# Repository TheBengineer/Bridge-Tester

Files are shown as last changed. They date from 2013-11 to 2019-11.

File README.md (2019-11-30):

Bridge-Tester
=============

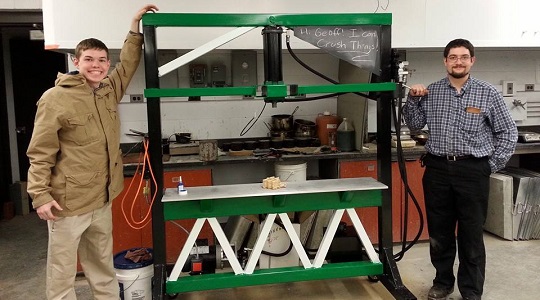
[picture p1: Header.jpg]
Project Image Project Picture


An Open Source bridge tester for popsicle stick bridge competitions.

This was my senior project at Vermont Technical College along with [Carter](
https://github.com/R8driver)

We designed this bridge crusher to be able to crush bridges of up to one meter long, while measuring characturistics about their weight.

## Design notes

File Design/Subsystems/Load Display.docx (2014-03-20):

# I²C Five Digit 7-Segment Display

Ben Holleran March 13, 2014

The following document details how the 7-segment display for the Gordonator bridge tester was designed, and works.

# Table of Contents

# Project Overview

The Gordonator bridge tester is an electro-mechanical senior project at Vermont Technical College. The goal of the project is to build a machine that can measure the force needed to break structures designed by the civil department, Specifically bridges constructed with popsicle sticks with a one meter span. The tester will be capable of replicating the Troitsky Bridge Building Competition at the Concordia University in Canada.

The Load Display subsystem will be displaying the force exerted on the bridge by the piston. Since the expected load is in excess of 9,999 LB, and less than 99,999 LB the display will have 5 digits. The display will also have 4” letters so the winning number can be seen from the back of the room.

# System Overview

## System Diagram

## System Description

As seen in the above system diagram, the display will be broken into 5 identical systems, each with a different IIC address. Each cell will have a single 7-segment display and the circuit needed to drive it. This will allow for easy replacement, and ease of design.

## Design Process

## Inception

The first step in the design process for the Load Display was its inception. There needed to be some form of a display to show the crowds how much force each bridge could hold. Some competitions do not need a load display, specifically high school competitions where weight of some kind is added incrementally until the bridge breaks. The weight can then be added up empirically by measuring the amount of water, or counting up how many weights were added. Since this tester will be using a hydraulic cylinder to provide force, allowing much higher loads than practical by the added weight method, there needs to be a display.

Research

The current tester at the Troitsky Bridge Building Competition was researched, and found to have a display only 1” high. Numerous people who have attended the competition have expressed that the display is too small, and is not visible from the seating area.

The problem was discussed with fellow students, professors, Industry professionals, and all of that was held together with queries to Google.

While researching current existing technology a few interesting discoveries were made:

- Many 2” and 3” clocks exist premade, but as clocks only have 4 digits.
- Many of the chips designed to run 7 segment displays are designed to run clocks.
- There are large numerical displays that are not clocks, but they are very expensive. The cheapest being around $500
- DigiKey sells individual 7 segments of all sizes.
- Texas instruments makes a nice IIC shift register suitable for running a single digit.

While researching communications it was determined that there were a few different technologies that were suitable.

- Serial
  - Single receiver, would require a MUX to run the separate digits
  - Very easy to use
- IIC
  - Multiple receivers
  - More difficult to use
- Direct IO
  - Easy to use
  - Needs a complicated circuit
  - Not enough pins

Brainstorming

After the available technologies were researched, the design was brainstormed to determine the best way to build the load display. It was determined that there were not enough pins on the Pi to do Direct IO and that a MUX circuit would be harder to make than the other available solutions. Serial was disqualified since it can have only one receiver, and that would make that receiver need to have enough pins to run all the displays, bringing back the Direct IO problem. There is multi receiver serial, but if going that route, IIC makes for a much better solution since it is in essence multi receiver serial, with the protocols already in place.

At one point it was considered to rate each system based on a number of criteria and pick the best one numerically, but those charts tend to be bullshit, so we just discussed the systems until it was clear which ones were less favorable, and then made an educated gut decision.

In the case of displays, it was originally thought that the best way to make a display would be to make the 7-segments from scratch using 5mm LEDs and large circuit boards. This was dismissed as too complicated and time consuming. Hacking a Walmart display was considered to be a bad idea in general, and all in all, the best solution seemed to be to buy premade 7-segments.

## Analysis

Once the 7-segments were chosen, the forward voltages of the LED arrays were measured and plotted on a Gaussian bell curve. This was then used to get a statistical voltage for the displays, allowing a more accurate current limiting resistor to be added.

The Datasheet said that the forward voltage on the 7-segents might be as low as 8V, meaning the resistor would have 4V from the 12V line across it. The calculated value to regulate to 60mA meant that if the forward voltage of the LEDs was 10V, the upper limit in the datasheet, there would only be 30mA going through the LEDs. This would significantly cut down on visibility. By using the voltage determined from the Gaussian bell curve, a resistor value was found that would put 70% of the LEDs at 50mA while being 90% sure that no LED would have over 60mA

Design

It was determined that the best way to construct a Load display would be to purchase 4” 7-segment displays from DigiKey, buy an IIC 7-segment driver chip from TI, create a board to connect everything, and then use a Python program running on the Pi to tell it what number to display over IIC.

## Testing

Once the Raspberry Pi was up and running, testing began on the chips and 7 segment displays. At first there were many unknown errors. Many of them proved to be problems with understanding of the IIC bus and driver issues on the Pi, but those were quickly sorted out. One of the more difficult errors to track down was a bad solder joint on the surface mount driver chips. After this discovery, all pins on all the chips were resoldered by hand and individually checked for continuity and shorting.

## Documentation

At all stages of the process, notes were taken in a project notebook. Some documentation for code was added to the GIT repository as commits. These comments were clear so that when looked at later, they would be easily understood.

## Project Management

Most of the project management: Task assignment, issue tracking, timeline, and file management, was all done by GitHub, a free online project management website. This tool will continue to be used throughout the project and will allow other people interesting in the design of the project to see what decisions were made.

# Conclusion

This subsystem is on track to being finished for its integration with the main project. The goal is to have a rock solid subsystem, so that any issues will be from its integration to the rest of the system, rather than issues with the subsystem itself.

I²C Five Digit 7-Segment Display Ben Holleran March 13, 2014

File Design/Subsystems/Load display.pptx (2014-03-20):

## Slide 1

88888

Load display

Power

IIC data line

GPIO Buffer

Raspberry PI

Single Digit

8

IIC Shift Register
TIPC2810

12 V

5 V

Individual segments. Switched to ground and current limited.

GND

IIC lines

Chip has 3 bits to program address. Need 5 addresses, one for each digit.

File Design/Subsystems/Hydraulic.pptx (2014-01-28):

## Symbols

Hydraulic
Motor

Pump

Cylinder

Reservoir

Pressure Relief

Check Valve

Filter

Valve

## Hydraulic Subsystem

1 ½ NPT

Valve has built in pressure relief

¾ NPT

½ NPT

¾-16

¼ NPT

Pressure Sensor

## Fittings List

1 ½ NPT

¾ NPT

½ NPT

¾-16

¼ NPT

Valve has built in pressure relief

Male to Male

½ - ½ - ¼ T

Pressure Sensor

5” pipe

¾ -16 m > ¾ NPT M

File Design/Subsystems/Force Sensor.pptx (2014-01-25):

## Force Sensor Subsystem Diagram

+12V

I²C ADC
24 bit

To I²C Master

Sensor

Address Config

¼ NPT

## Force Sensor Subsystem Schematic

+12V

I²C ADC
24 bit

Sensor

¼ NPT

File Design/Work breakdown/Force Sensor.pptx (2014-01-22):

## Force Sensor Subsystem Diagram

To Piston

I²C A to D Converter

Pressure Sensor

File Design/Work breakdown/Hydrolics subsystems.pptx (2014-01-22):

## Hydraulics Subsystem

Pump

Piston

Switch

Pressure Sensor

Pressure relief Valve

Motor

Reservoir

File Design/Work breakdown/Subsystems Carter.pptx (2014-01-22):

## Work Breakdown

Areas of Responsibility | | | | Mechanical
Ben | | Carter | | Electrical
Hydraulics | | Frame | | Software
Force Sensor | | Monitor and 7-Segment
HDMI Display GUI | | HDMI Display GUI
Mounting Points on Frame | | Mounting Points on Frame
Website | | Website

## Frame

Final top structure design pending on cylinder used

Exostructure made of 3in hollow steel tubing

40in span between trusses for Troisky compatible bridges and max strength

40in

3 triangular trusses for structural support made of 2in hollow steel tubing

Wheels for easy mobility of unit

## Hydraulics Subsystem

Pump

Piston

Switch

Pressure Sensor

Pressure relief Valve

Motor

Reservoir

## 7-Segment Display Subsystem

V+ ~20V

7-Seg
Digit

X5

Input from Pi
Over GPIO

I2C
7-Seg Driver

7-Seg Driver requires 11V forward. I2C driver outputs 5V. Darlington Array is used to boost voltage to 7-Segment Digits.

Darlington Array

Ground

## LCD Monitor Subsystem

Inputs from sensors

Raspberry Pi

GPIO

Deformation

HDMI

READOUTS

Force

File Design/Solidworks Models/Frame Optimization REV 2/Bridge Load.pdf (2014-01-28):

Vermont technical College
Company Address Line 2]

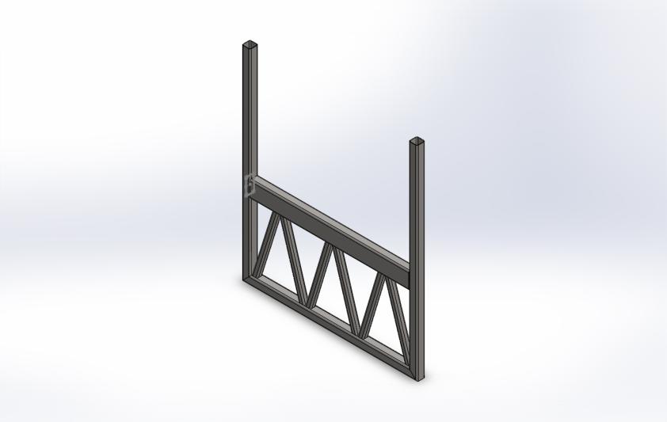
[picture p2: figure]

Analyzed with SolidWorks Simulation | Simulation of Main Frame | 1

# Simulation of Main Frame

Date: Wednesday, January 22, 2014 Designer: Carter Mealey, Ben Holleran Study name: Bridge
Analysis type: Static

## Table of Contents

## Description

No Data

Vermont technical College | Carter Mealey, Ben Holleran

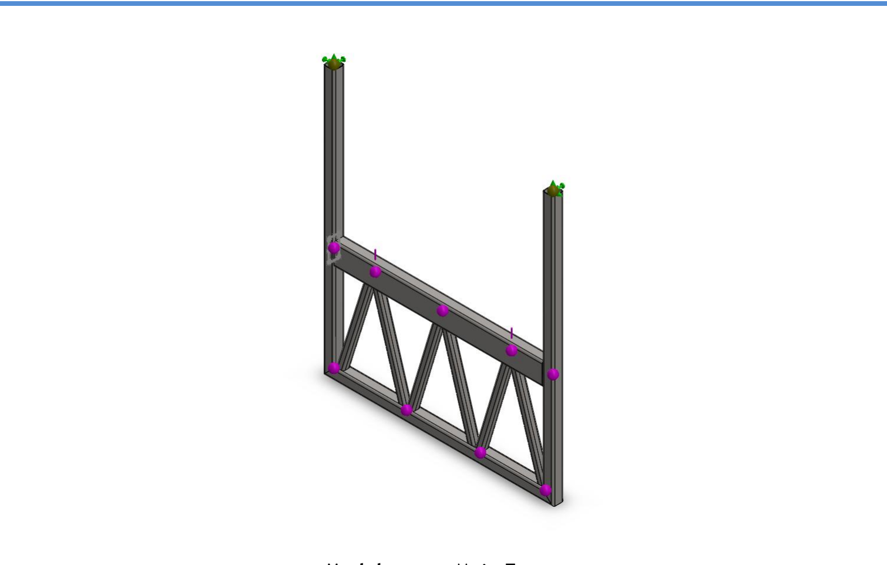
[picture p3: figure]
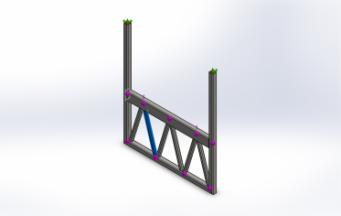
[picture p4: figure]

Analyzed with SolidWorks Simulation | Simulation of Main Frame | 2

## Assumptions

## Model Information

Model name: Main Frame
Current Configuration: Default<As Machined>

### Beam Bodies:

Document Name and Reference | Formulation | Properties | Document Path/Date Modified
Beam-1(Truss Trim[2]) | Beam – Uniform C/S | Section Standard-Section Area: 544.265in^2 Length:636.35mm Volume:0.000346335m^3 Mass Density:7800kg/m^3 Mass:2.70141kg Weight:26.4738N | \\vtcfiles\shared\ELM\ELM 4701\Bridge Tester\Design\Solidworks Models\Frame Optimization REV 2\Main Frame.SLDPRT Jan 22 00:54:07 2014

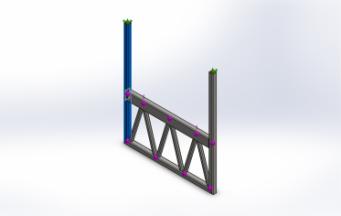
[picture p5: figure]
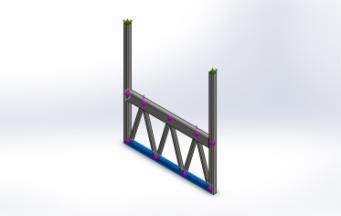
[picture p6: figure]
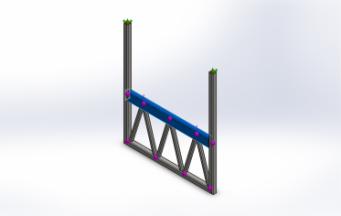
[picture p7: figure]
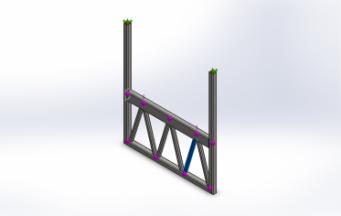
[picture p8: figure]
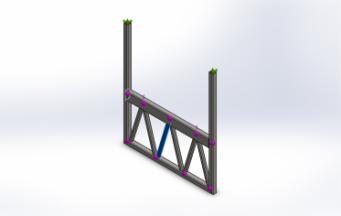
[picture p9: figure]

Analyzed with SolidWorks Simulation | Simulation of Main Frame | 3
Beam-2(Bottom miter 2[2]) | Beam – Uniform C/S | Section Standard-ansi inch/square tube/3 x 3 x 0.25 Section Area: 866.845in^2 Length:1828.8mm Volume:0.00158529m^3 Mass Density:7800kg/m^3 Mass:12.3652kg Weight:121.179N | \\vtcfiles\shared\ELM\ELM 4701\Bridge Tester\Design\Solidworks Models\Frame Optimization REV 2\Main Frame.SLDPRT Jan 22 00:54:07 2014
Beam-3(Bottom miter 2[1]) | Beam – Uniform C/S | Section Standard-ansi inch/square tube/3 x 3 x 0.25 Section Area: 1670.35in^2 Length:1524mm Volume:0.00254566m^3 Mass Density:7800kg/m^3 Mass:19.8561kg Weight:194.59N | \\vtcfiles\shared\ELM\ELM 4701\Bridge Tester\Design\Solidworks Models\Frame Optimization REV 2\Main Frame.SLDPRT Jan 22 00:54:07 2014
Beam-4(Deck trim) | Beam – Uniform C/S | Section Standard-ansi inch/rectangular tube/3 x 2 x 0.25 Section Area: 1350.71in^2 Length:1447.8mm Volume:0.00195556m^3 Mass Density:7800kg/m^3 Mass:15.2534kg Weight:149.483N | \\vtcfiles\shared\ELM\ELM 4701\Bridge Tester\Design\Solidworks Models\Frame Optimization REV 2\Main Frame.SLDPRT Jan 22 00:54:07 2014
Beam-5(Truss Trim[5]) | Beam – Uniform C/S | Section Standard-Section Area: 544.265in^2 Length:636.35mm Volume:0.000346335m^3 Mass Density:7800kg/m^3 Mass:2.70141kg Weight:26.4738N | \\vtcfiles\shared\ELM\ELM 4701\Bridge Tester\Design\Solidworks Models\Frame Optimization REV 2\Main Frame.SLDPRT Jan 22 00:54:07 2014
Beam-6(Truss Trim[3]) | Beam – Uniform C/S | Section Standard-Section Area: 544.265in^2 Length:636.35mm Volume:0.000346335m^3 Mass Density:7800kg/m^3 Mass:2.70141kg Weight:26.4738N | \\vtcfiles\shared\ELM\ELM 4701\Bridge Tester\Design\Solidworks Models\Frame Optimization REV 2\Main Frame.SLDPRT Jan 22 00:54:07 2014

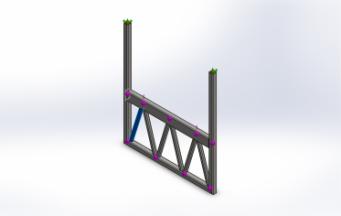
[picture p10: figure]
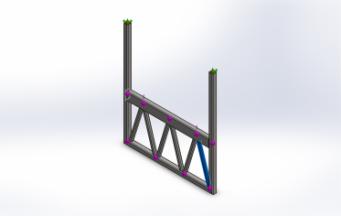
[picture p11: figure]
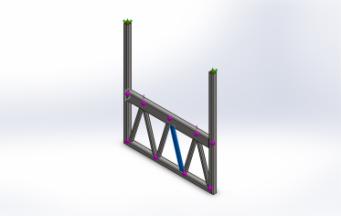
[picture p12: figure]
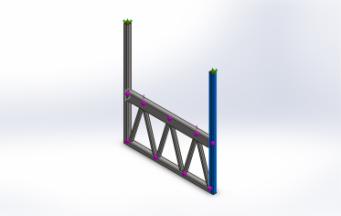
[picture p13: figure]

Analyzed with SolidWorks Simulation | Simulation of Main Frame | 4
Beam-7(Truss Trim[1]) | Beam – Uniform C/S | Section Standard-Section Area: 544.265in^2 Length:638.672mm Volume:0.000347599m^3 Mass Density:7800kg/m^3 Mass:2.71127kg Weight:26.5704N | \\vtcfiles\shared\ELM\ELM 4701\Bridge Tester\Design\Solidworks Models\Frame Optimization REV 2\Main Frame.SLDPRT Jan 22 00:54:07 2014
Beam-8(Truss Trim[6]) | Beam – Uniform C/S | Section Standard-Section Area: 544.265in^2 Length:638.672mm Volume:0.000347599m^3 Mass Density:7800kg/m^3 Mass:2.71127kg Weight:26.5704N | \\vtcfiles\shared\ELM\ELM 4701\Bridge Tester\Design\Solidworks Models\Frame Optimization REV 2\Main Frame.SLDPRT Jan 22 00:54:07 2014
Beam-9(Truss Trim[4]) | Beam – Uniform C/S | Section Standard-Section Area: 544.265in^2 Length:636.35mm Volume:0.000346335m^3 Mass Density:7800kg/m^3 Mass:2.70141kg Weight:26.4738N | \\vtcfiles\shared\ELM\ELM 4701\Bridge Tester\Design\Solidworks Models\Frame Optimization REV 2\Main Frame.SLDPRT Jan 22 00:54:07 2014
Beam-10(Bottom miter 1[2]) | Beam – Uniform C/S | Section Standard-ansi inch/square tube/3 x 3 x 0.25 Section Area: 866.845in^2 Length:1828.8mm Volume:0.00158529m^3 Mass Density:7800kg/m^3 Mass:12.3652kg Weight:121.179N | \\vtcfiles\shared\ELM\ELM 4701\Bridge Tester\Design\Solidworks Models\Frame Optimization REV 2\Main Frame.SLDPRT Jan 22 00:54:07 2014

Analyzed with SolidWorks Simulation | Simulation of Main Frame | 5

## Study Properties

Study name | Bridge
Analysis type | Static
Mesh type | Beam Mesh
Solver type | Direct sparse solver
Inplane Effect: | Off
Soft Spring: | Off
Inertial Relief: | Off
Incompatible bonding options | Automatic
Large displacement | Off
Compute free body forces | On
Result folder | SolidWorks document (\\vtcfiles\shared\ELM\ELM4701\Bridge Tester\Design\Solidworks Models\Frame Optimization REV 2)

## Units

Unit system: | SI (MKS)
Length/Displacement | mm
Temperature | Kelvin
Angular velocity | Rad/sec
Pressure/Stress | N/m^2

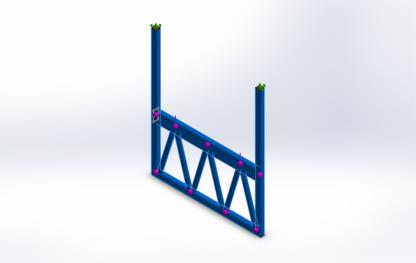
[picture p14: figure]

Analyzed with SolidWorks Simulation | Simulation of Main Frame | 6

## Material Properties

Model Reference | Properties | Components
| Name: Plain Carbon Steel Model type: Linear Elastic Isotropic Default failure criterion: Unknown
| Yield strength: 2.20594e+008 N/m^2 Tensile strength: 3.99826e+008 N/m^2 Elastic modulus: 2.1e+011 N/m^2 Poisson's ratio: 0.28 Mass density: 7800 kg/m^3 Shear modulus: 7.9e+010 N/m^2 Thermal expansion coefficient: 1.3e-005 /Kelvin

SolidBody 1(Truss
Trim[2])(Main Frame),
SolidBody 2(Bottom miter
2[2])(Main Frame),
SolidBody 3(Bottom miter
2[1])(Main Frame),
SolidBody 4(Deck trim)(Main Frame),
SolidBody 5(Truss
Trim[5])(Main Frame),
SolidBody 6(Truss
Trim[3])(Main Frame),
SolidBody 7(Truss
Trim[1])(Main Frame),
SolidBody 8(Truss
Trim[6])(Main Frame),
SolidBody 9(Truss
Trim[4])(Main Frame),
SolidBody 10(Bottom miter
1[2])(Main Frame)

Curve Data:N/A

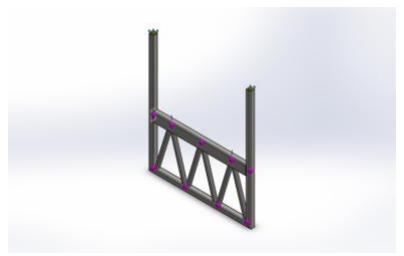
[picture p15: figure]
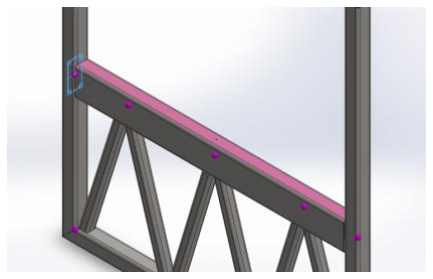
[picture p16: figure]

Analyzed with SolidWorks Simulation | Simulation of Main Frame | 7

## Loads and Fixtures

Fixture name | Fixture Image | Fixture Details

Fixed-1

Entities: 2 Joint(s)
Type: Fixed Geometry
Load name | Load Image | Load Details

Force-1

Entities: 2 Joint(s)
Reference: Face< 1 >
Type: Apply force
Values: ---, ---, 10000 lbf Moments: ---, ---, --- lbf·in

## Connector Definitions

No Data

## Contact Information

No Data

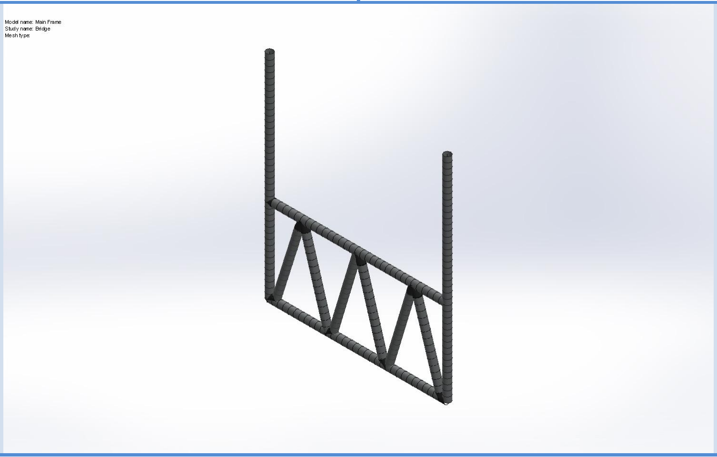
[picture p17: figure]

Analyzed with SolidWorks Simulation | Simulation of Main Frame | 8

## Mesh Information

Mesh type | Beam Mesh

### Mesh Information - Details

Total Nodes | 247
Total Elements | 243
Time to complete mesh(hh;mm;ss): | 00:00:02
Computer name: | DRACOLYTH

Analyzed with SolidWorks Simulation | Simulation of Main Frame | 9

## Sensor Details

No Data

## Resultant Forces

### Reaction Forces

Selection set | Units | Sum X | Sum Y | Sum Z | Resultant
Entire Model | N | 0 | 88964.4 | 4.38451e-016 | 88964.4

### Reaction Moments

Selection set | Units | Sum X | Sum Y | Sum Z | Resultant
Entire Model | N·m | -1.54772e-013 | 7.4997e-012 | 9.06491 | 9.06491

Analyzed with SolidWorks Simulation | Simulation of Main Frame | 10

## Beams

### Beam Forces

Beam Name | Joints | Axial(N) | Shear1(N) | Shear2(N) | Moment1(N·m) | Moment2(N·m) | Torque(N·m)
Beam-1(Truss Trim[2]) | 1 | 5504.27 | 0.00138841 | -559.878 | -160.011 | -0.000396805 | -1.46155e-013
| 2 | -5504.27 | -0.000956741 | 559.881 | -218.535 | -0.00037344 | 1.46153e-013
Beam-2(Bottom miter 2[2]) | 1 | 44488.2 | -4.91304e-012 | -786.007 | -284.243 | 3.04103e-012 | 3.80117e-012
| 2 | -28586.1 | -9.50966e-013 | 2739.79 | -933.427 | -7.68225e-013 | -3.02452e-014
| 3 | 28586.1 | 9.50966e-013 | -2739.79 | -1049.9 | 7.9821e-014 | 3.02453e-014
Beam-3(Bottom miter 2[1]) | 1 | 12499.6 | -230.882 | -4.82211e-013 | -3.8713e-013 | 326.435 | 6.70304e-013
| 2 | -12499.6 | 230.882 | -8.06557e-012 | -1.70118e-012 | -220.413 | -5.54059e-013
| 3 | 16330.9 | -22.2372 | -2.2299e-013 | -1.09055e-013 | 308.642 | 5.57374e-013
| 4 | 12502.8 | 141.669 | -1.85641e-013 | 6.03742e-014 | 282.03 | 1.82823e-013
Beam-4(Deck trim) | 1 | -1953.78 | -15902 | 4.46363e-012 | -2.35418e-012 | 2950.9 | 2.58243e-012
| 2 | 1953.78 | 15902 | -4.46363e-012 | 3.47111e-012 | 1028.25 | -2.58243e-012
| 3 | -13822.2 | -5278.18 | 4.70448e-012 | 2.24511e-012 | 2625.31 | 2.08829e-012
| 4 | -13829 | 5337.22 | 5.65953e-012 | 4.13361e-013 | 147.18 | 1.81326e-012
| 5 | -1839.42 | 15563.5 | 5.32308e-012 | 3.39428e-012 | -1571.08 | 1.30878e-012
Beam-5(Truss Trim[5]) | 1 | -5518.91 | -0.00366016 | 544.99 | -154.805 | -0.00103967 | 1.00083e-014
| 2 | 0 | 0 | 0 | 0 | 0 | 0
Beam-6(Truss Trim[3]) | 1 | 5589.51 | -0.00063585 | -117.228 | 57.8102 | -0.000313564 | 1.39206e-013
| 2 | -5589.51 | -0.000419664 | 117.23 | 26.1154 | 9.34892e-005 | -1.39204e-013
Beam-7(Truss Trim[1]) | 1 | -29975.6 | -0.00194658 | 857.857 | 273.025 | 0.000619527 | -9.09229e-014
| 2 | 29975.6 | 0.000763378 | -857.871 | 274.871 | 0.000244594 | 9.09231e-014
Beam-8(Truss Trim[6]) | 1 | -30407.6 | -1.02897e-014 | 846.037 | 271.294 | 1.57306e-013 | -1.57159e-013
| 2 | 30407.6 | 0.000182593 | -846.037 | 269.046 | 5.80658e-005 | 1.57159e-013
9(Truss Beam- | 1 | -5566.14 | -0.000188081 | 131.381 | 59.3665 | 8.49869e-005 | -2.4356e-013

Analyzed with SolidWorks Simulation | Simulation of Main Frame | 11
Trim[4]) | 2 | 5566.14 | 0.00115671 | -131.388 | 24.2387 | 0.000213391 | 2.4356e-013
Beam-10(Bottom miter 1[2]) | 1 | -28912.8 | 4.80964e-013 | -2625.44 | 904.625 | -6.34336e-013 | -3.04245e-013
| 2 | 44476.3 | 0.0166265 | 785.892 | 293.308 | -0.00620528 | 3.69852e-012
| 3 | 28912.8 | -4.80964e-013 | 2625.44 | 877.148 | 9.60745e-013 | 3.04245e-013

### Beam Stresses

Beam Name | Joints | Axial(N/m^2) | Bending Dir1(N/m^2) | Bending Dir2(N/m^2) | Torsional (N/m^2) | Worst Case(N/m^2)
Beam-1(Truss Trim[2]) | 1 | 1.01132e+007 | -2.13806e+007 | 53.0208 | -7.77954e-009 | 3.14939e+007
| 2 | 1.01132e+007 | 2.92006e+007 | -49.8988 | 7.77945e-009 | 3.93138e+007
Beam-2(Bottom miter 2[2]) | 1 | 5.1322e+007 | -1.46963e+007 | -1.57232e-007 | 8.22346e-008 | 6.60183e+007
| 2 | 3.29772e+007 | 4.82614e+007 | -3.97199e-008 | -6.54326e-010 | 8.12386e+007
| 3 | 3.29772e+007 | -5.42837e+007 | -4.12702e-009 | 6.54327e-010 | 8.72609e+007
Beam-3(Bottom miter 2[1]) | 1 | 7.48321e+006 | -1.12285e-008 | -9.4681e+006 | 1.45014e-008 | 1.69513e+007
| 2 | 7.48321e+006 | 4.93421e-008 | -6.39299e+006 | -1.19865e-008 | 1.38762e+007
| 3 | 9.77695e+006 | -3.1631e-009 | -8.95204e+006 | 1.20582e-008 | 1.8729e+007
| 4 | 7.48514e+006 | 1.75113e-009 | -8.18017e+006 | 3.95519e-009 | 1.56653e+007
Beam-4(Deck trim) | 1 | -1.44648e+006 | -6.4884e-008 | -5.63782e+007 | 3.31982e-008 | 5.78247e+007
| 2 | -1.44648e+006 | -9.56679e-008 | 1.96452e+007 | -3.31982e-008 | 2.10917e+007
| 3 | -1.02332e+007 | 6.1878e-008 | -5.01576e+007 | 2.68459e-008 | 6.03908e+007
| 4 | -1.02383e+007 | 1.13927e-008 | -2.81194e+006 | 2.33102e-008 | 1.30503e+007
| 5 | -1.36181e+006 | 9.35504e-008 | 3.00162e+007 | 1.6825e-008 | 3.1378e+007
Beam-5(Truss Trim[5]) | 1 | 1.01401e+007 | 2.06849e+007 | -138.92 | 5.32722e-010 | 3.08252e+007
| 2 | 0 | 0 | 0 | 0 | 0
Beam-6(Truss Trim[3]) | 1 | -1.02698e+007 | -7.72456e+006 | -41.8982 | 7.40965e-009 | 1.79944e+007
| 2 | -1.02698e+007 | 3.48953e+006 | -12.492 | -7.40958e-009 | 1.37594e+007
Beam-7(Truss Trim[1]) | 1 | -5.50755e+007 | 3.64814e+007 | -82.7808 | -4.83965e-009 | 9.1557e+007
| 2 | -5.50755e+007 | -3.67281e+007 | 32.6826 | 4.83966e-009 | 9.18036e+007
Beam-8(Truss Trim[6]) | 1 | -5.58692e+007 | 3.62501e+007 | -2.10191e-008 | -8.36525e-009 | 9.21193e+007
| 2 | -5.58692e+007 | -3.59498e+007 | 7.75872 | 8.36525e-009 | 9.1819e+007
Beam-9(Truss Trim[4]) | 1 | -1.02269e+007 | 7.93251e+006 | -11.3559 | -1.29643e-008 | 1.81594e+007
| 2 | -1.02269e+007 | -3.23876e+006 | 28.5132 | 1.29642e-008 | 1.34657e+007
Beam-10(Bottom miter 1[2]) | 1 | 3.33541e+007 | -4.67722e+007 | -3.27974e-008 | -6.58205e-009 | 8.01263e+007
| 2 | 5.13082e+007 | 1.5165e+007 | 320.834 | 8.00139e-008 | 6.64736e+007
| 3 | 3.33541e+007 | 4.53516e+007 | -4.96739e-008 | 6.58205e-009 | 7.87057e+007

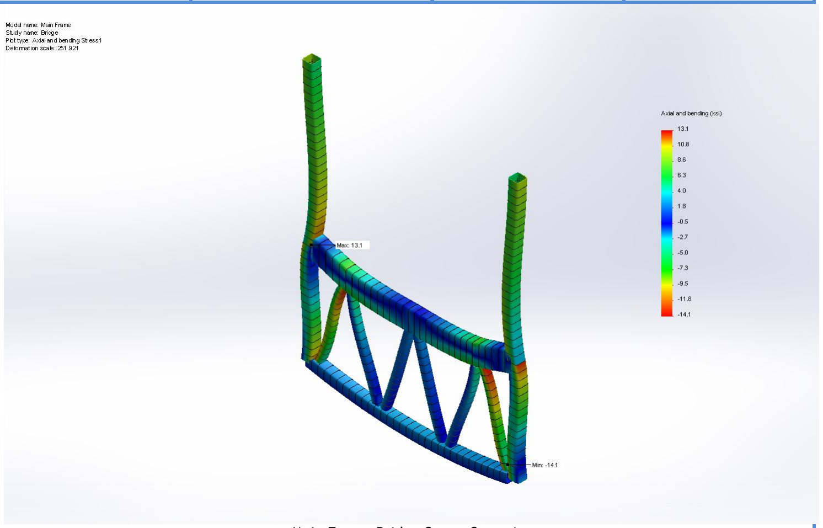
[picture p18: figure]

Analyzed with SolidWorks Simulation | Simulation of Main Frame | 12

## Study Results

Name | Type | Min | Max
Stress1 | TXY: Shear in Y Dir. on YZ Plane | 0 ksi Element: 233 | 13.3608 ksi Element: 178

Main Frame-Bridge-Stress-Stress1

Name | Type | Min | Max
Displacement1 | URES: Resultant Displacement | 0 in Node: 57 | 0.0285959 in Node: 107

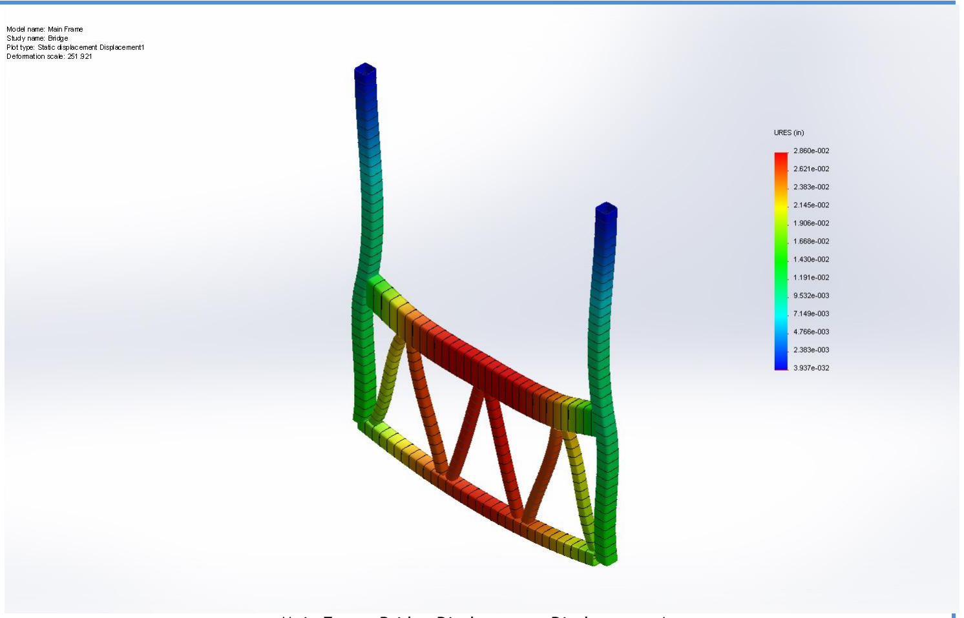
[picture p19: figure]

Analyzed with SolidWorks Simulation | Simulation of Main Frame | 13

Main Frame-Bridge-Displacement-Displacement1

Name | Type
Displacement1{1} | Deformed Shape

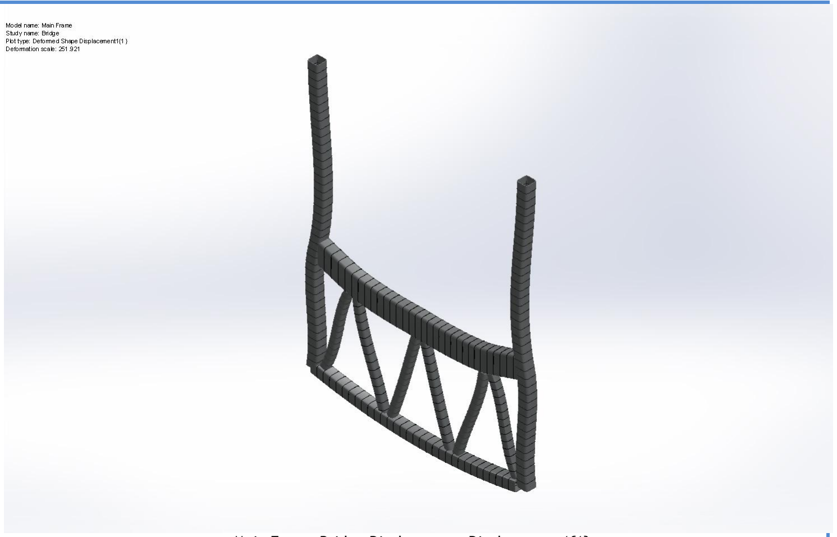
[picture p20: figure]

Analyzed with SolidWorks Simulation | Simulation of Main Frame | 14

Main Frame-Bridge-Displacement-Displacement1{1}

Name | Type | Min | Max
Factor of Safety1 | Automatic | 2.39465 Node: 181 | 20.0803 Node: 148

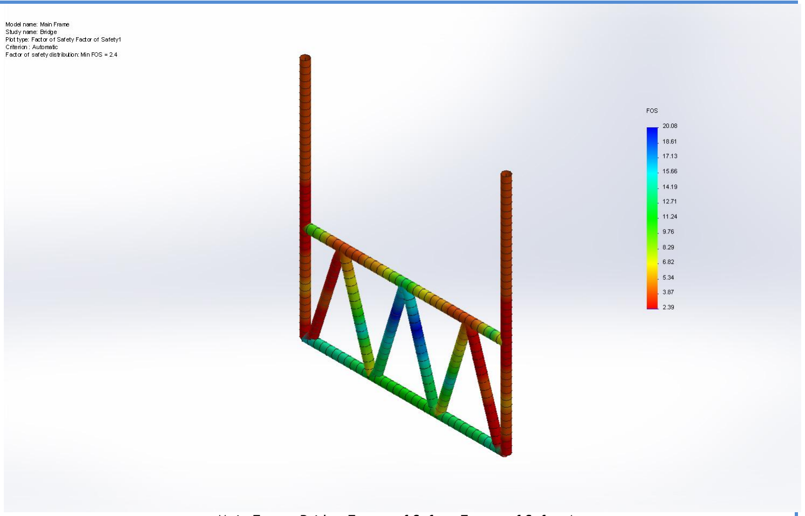
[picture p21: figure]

Analyzed with SolidWorks Simulation | Simulation of Main Frame | 15

Main Frame-Bridge-Factor of Safety-Factor of Safety1

## Conclusion

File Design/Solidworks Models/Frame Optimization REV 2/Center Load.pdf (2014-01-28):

Vermont Technical College
Company Address Line 2]

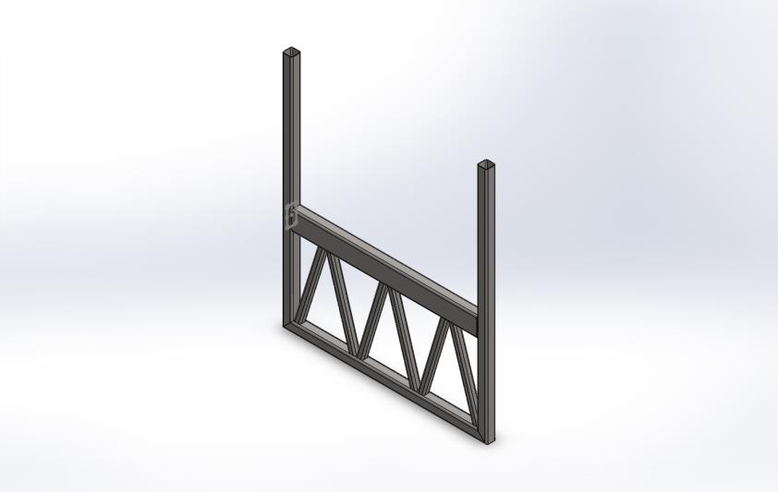
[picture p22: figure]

Analyzed with SolidWorks Simulation | Simulation of Main Frame | 1

# Simulation of Main Frame

Date: Wednesday, January 22, 2014 Designer: Carter Mealey, Ben Holleran Study name: Center Load
Analysis type: Static

## Table of Contents

## Description

No Data

Vermont Technical College | Carter Mealey, Ben Holleran

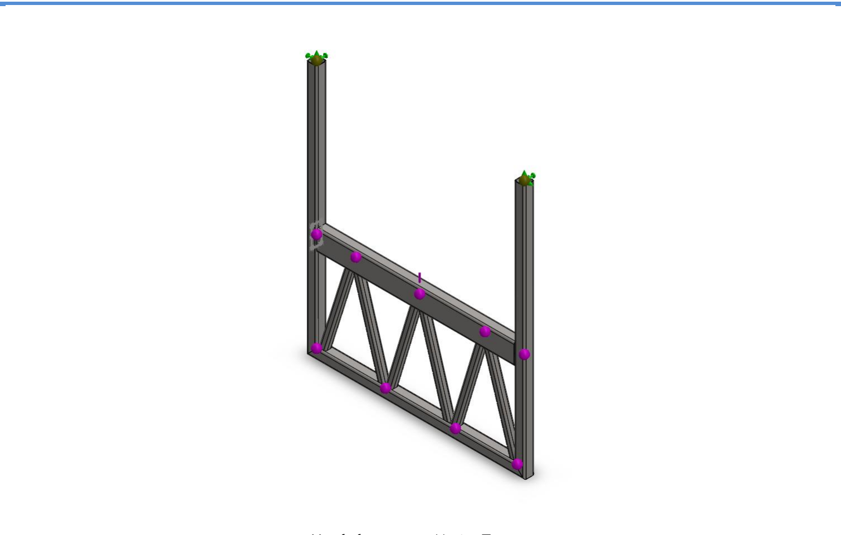
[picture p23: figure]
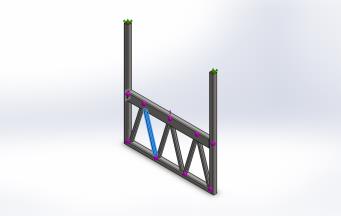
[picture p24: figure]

Analyzed with SolidWorks Simulation | Simulation of Main Frame | 2

## Assumptions

## Model Information

Model name: Main Frame
Current Configuration: Default<As Machined>

### Beam Bodies:

Document Name and Reference | Formulation | Properties | Document Path/Date Modified
Beam-1(Truss Trim[2]) | Beam – Uniform C/S | Section Standard-Section Area: 544.265in^2 Length:636.35mm Volume:0.000346335m^3 Mass Density:7800kg/m^3 Mass:2.70141kg Weight:26.4738N | \\vtcfiles\shared\ELM\ELM 4701\Bridge Tester\Design\Solidworks Models\Frame Optimization REV 2\Main Frame.SLDPRT Jan 22 00:54:07 2014

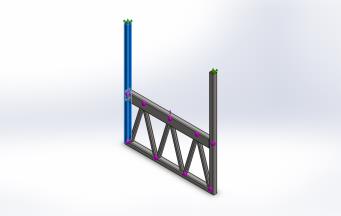
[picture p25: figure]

Analyzed with SolidWorks Simulation | Simulation of Main Frame | 3
Beam-2(Bottom miter 2[2]) | Beam – Uniform C/S | Section Standard-ansi inch/square tube/3 x 3 x 0.25 Section Area: 866.845in^2 Length:1828.8mm Volume:0.00158529m^3 Mass Density:7800kg/m^3 Mass:12.3652kg Weight:121.179N | \\vtcfiles\shared\ELM\ELM 4701\Bridge Tester\Design\Solidworks Models\Frame Optimization REV 2\Main Frame.SLDPRT Jan 22 00:54:07 2014
Beam-3(Bottom miter 2[1]) | Beam – Uniform C/S | Section Standard-ansi inch/square tube/3 x 3 x 0.25 Section Area: 1670.35in^2 Length:1524mm Volume:0.00254566m^3 Mass Density:7800kg/m^3 Mass:19.8561kg Weight:194.59N | \\vtcfiles\shared\ELM\ELM 4701\Bridge Tester\Design\Solidworks Models\Frame Optimization REV 2\Main Frame.SLDPRT Jan 22 00:54:07 2014
Beam-4(Deck trim) | Beam – Uniform C/S | Section Standard-ansi inch/rectangular tube/3 x 2 x 0.25 Section Area: 1350.71in^2 Length:1447.8mm Volume:0.00195556m^3 Mass Density:7800kg/m^3 Mass:15.2534kg Weight:149.483N | \\vtcfiles\shared\ELM\ELM 4701\Bridge Tester\Design\Solidworks Models\Frame Optimization REV 2\Main Frame.SLDPRT Jan 22 00:54:07 2014
Beam-5(Truss Trim[5]) | Beam – Uniform C/S | Section Standard-Section Area: 544.265in^2 Length:636.35mm Volume:0.000346335m^3 Mass Density:7800kg/m^3 Mass:2.70141kg Weight:26.4738N | \\vtcfiles\shared\ELM\ELM 4701\Bridge Tester\Design\Solidworks Models\Frame Optimization REV 2\Main Frame.SLDPRT Jan 22 00:54:07 2014
Beam-6(Truss Trim[3]) | Beam – Uniform C/S | Section Standard-Section Area: 544.265in^2 Length:636.35mm Volume:0.000346335m^3 Mass Density:7800kg/m^3 Mass:2.70141kg Weight:26.4738N | \\vtcfiles\shared\ELM\ELM 4701\Bridge Tester\Design\Solidworks Models\Frame Optimization REV 2\Main Frame.SLDPRT Jan 22 00:54:07 2014


Analyzed with SolidWorks Simulation | Simulation of Main Frame | 4
Beam-7(Truss Trim[1]) | Beam – Uniform C/S | Section Standard-Section Area: 544.265in^2 Length:638.672mm Volume:0.000347599m^3 Mass Density:7800kg/m^3 Mass:2.71127kg Weight:26.5704N | \\vtcfiles\shared\ELM\ELM 4701\Bridge Tester\Design\Solidworks Models\Frame Optimization REV 2\Main Frame.SLDPRT Jan 22 00:54:07 2014
Beam-8(Truss Trim[6]) | Beam – Uniform C/S | Section Standard-Section Area: 544.265in^2 Length:638.672mm Volume:0.000347599m^3 Mass Density:7800kg/m^3 Mass:2.71127kg Weight:26.5704N | \\vtcfiles\shared\ELM\ELM 4701\Bridge Tester\Design\Solidworks Models\Frame Optimization REV 2\Main Frame.SLDPRT Jan 22 00:54:07 2014
Beam-9(Truss Trim[4]) | Beam – Uniform C/S | Section Standard-Section Area: 544.265in^2 Length:636.35mm Volume:0.000346335m^3 Mass Density:7800kg/m^3 Mass:2.70141kg Weight:26.4738N | \\vtcfiles\shared\ELM\ELM 4701\Bridge Tester\Design\Solidworks Models\Frame Optimization REV 2\Main Frame.SLDPRT Jan 22 00:54:07 2014
Beam-10(Bottom miter 1[2]) | Beam – Uniform C/S | Section Standard-ansi inch/square tube/3 x 3 x 0.25 Section Area: 866.845in^2 Length:1828.8mm Volume:0.00158529m^3 Mass Density:7800kg/m^3 Mass:12.3652kg Weight:121.179N | \\vtcfiles\shared\ELM\ELM 4701\Bridge Tester\Design\Solidworks Models\Frame Optimization REV 2\Main Frame.SLDPRT Jan 22 00:54:07 2014

Analyzed with SolidWorks Simulation | Simulation of Main Frame | 5

## Study Properties

Study name | Center Load
Analysis type | Static
Mesh type | Beam Mesh
Solver type | Direct sparse solver
Inplane Effect: | Off
Soft Spring: | Off
Inertial Relief: | Off
Incompatible bonding options | Automatic
Large displacement | Off
Compute free body forces | On
Result folder | SolidWorks document (\\vtcfiles\shared\ELM\ELM4701\Bridge Tester\Design\Solidworks Models\Frame Optimization REV 2)

## Units

Unit system: | SI (MKS)
Length/Displacement | mm
Temperature | Kelvin
Angular velocity | Rad/sec
Pressure/Stress | N/m^2


Analyzed with SolidWorks Simulation | Simulation of Main Frame | 6

## Material Properties

Model Reference | Properties | Components
| Name: Plain Carbon Steel Model type: Linear Elastic Isotropic Default failure criterion: Unknown
| Yield strength: 2.20594e+008 N/m^2 Tensile strength: 3.99826e+008 N/m^2 Elastic modulus: 2.1e+011 N/m^2 Poisson's ratio: 0.28 Mass density: 7800 kg/m^3 Shear modulus: 7.9e+010 N/m^2 Thermal expansion coefficient: 1.3e-005 /Kelvin

SolidBody 1(Truss
Trim[2])(Main Frame),
SolidBody 2(Bottom miter
2[2])(Main Frame),
SolidBody 3(Bottom miter
2[1])(Main Frame),
SolidBody 4(Deck trim)(Main Frame),
SolidBody 5(Truss
Trim[5])(Main Frame),
SolidBody 6(Truss
Trim[3])(Main Frame),
SolidBody 7(Truss
Trim[1])(Main Frame),
SolidBody 8(Truss
Trim[6])(Main Frame),
SolidBody 9(Truss
Trim[4])(Main Frame),
SolidBody 10(Bottom miter
1[2])(Main Frame)

Curve Data:N/A


Analyzed with SolidWorks Simulation | Simulation of Main Frame | 7

## Loads and Fixtures

Fixture name | Fixture Image | Fixture Details

Fixed-1

Entities: | 2 Joint(s)
Type: | Fixed Geometry
Load name | Load Image | Load Details

Force-1

Entities: | 1 Joint(s)
Reference: | Face< 1 >
Type: | Apply force
Values: | ---, ---, 20000 lbf
Moments: | ---, ---, --- lbf·in

## Connector Definitions

No Data

## Contact Information

No Data


Analyzed with SolidWorks Simulation | Simulation of Main Frame | 8

## Mesh Information

Mesh type | Beam Mesh

### Mesh Information - Details

Total Nodes | 247
Total Elements | 243
Time to complete mesh(hh;mm;ss): | 00:00:02
Computer name: | DRACOLYTH

Analyzed with SolidWorks Simulation | Simulation of Main Frame | 9

## Sensor Details

No Data

## Resultant Forces

## Reaction Forces

Selection set | Units | Sum X | Sum Y | Sum Z | Resultant
Entire Model | N | 0 | 88964.4 | 1.00571e-015 | 88964.4

## Reaction Moments

Selection set | Units | Sum X | Sum Y | Sum Z | Resultant
Entire Model | N·m | -2.60671e-012 | 9.61975e-012 | 9.82266 | 9.82266

Analyzed with SolidWorks Simulation | Simulation of Main Frame | 10

## Beams

## Beam Forces

Beam Name | Joints | Axial(N) | Shear1(N) | Shear2(N) | Moment1(N·m) | Moment2(N·m) | Torque(N·m)
Beam-1(Truss Trim[2]) | 1 | 35684.5 | 0.00285653 | -1151.89 | -358.37 | -0.000888705 | -8.21433e-014
| 2 | -35684.5 | -0.00196842 | 1151.91 | -420.459 | -0.000718492 | 8.21438e-014
Beam-2(Bottom miter 2[2]) | 1 | 44824.6 | -6.32148e-012 | -989.513 | -362.248 | 2.60767e-012 | 4.85129e-012
| 2 | -34512.5 | -9.03141e-013 | 3572.53 | -1257.57 | -1.8386e-013 | -1.87233e-013
| 3 | 34512.5 | 9.03141e-013 | -3572.53 | -1328.59 | -4.69924e-013 | 1.87233e-013
Beam-3(Bottom miter 2[1]) | 1 | 15702.1 | -592.01 | -2.90471e-014 | -5.78065e-013 | 257.328 | 1.99826e-013
| 2 | -15702.1 | 592.01 | 1.24046e-011 | 1.08368e-013 | 14.5242 | -2.05585e-013
| 3 | 37652.5 | -208.95 | 2.94847e-013 | -8.84075e-014 | 1021.94 | -5.44194e-014
| 4 | 15293.7 | 730.015 | -5.7622e-013 | 3.19106e-013 | 17.7887 | 6.66246e-013
Beam-4(Deck trim) | 1 | -2583.02 | -10312.1 | 5.39609e-012 | -2.64853e-012 | 913.636 | 3.5299e-012
| 2 | 2583.02 | 10312.1 | -5.39609e-012 | 3.99879e-012 | 1666.76 | -3.5299e-012
| 3 | -25710.2 | 9142.05 | 7.83309e-012 | 2.77223e-012 | 255.892 | 1.19263e-012
| 4 | -26053.7 | -10378.6 | 4.87719e-012 | -2.39271e-014 | 5014.47 | 2.67068e-012
| 5 | -2432.68 | 10235.5 | 6.88297e-012 | 4.31096e-012 | -1969.56 | 9.68686e-013
Beam-5(Truss Trim[5]) | 1 | -36099.5 | -0.00735709 | 1095.46 | -339.817 | -0.00228221 | -3.9553e-014
| 2 | 0 | 0 | 0 | 0 | 0 | 0
Beam-6(Truss Trim[3]) | 1 | 35841.5 | -0.00184985 | -341.046 | 173.333 | -0.000940165 | 1.10032e-013
| 2 | -35841.5 | -0.00122092 | 341.054 | 70.8359 | 0.000253582 | -1.10029e-013
Beam-7(Truss Trim[1]) | 1 | -35994.4 | -0.00331255 | 1459.84 | 483.596 | 0.00109734 | -1.2082e-013
| 2 | 35994.4 | 0.00129905 | -1459.85 | 448.768 | 0.000399337 | 1.2082e-013
Beam-8(Truss Trim[6]) | 1 | -35205.2 | 3.14319e-013 | 1436.05 | 445.132 | 3.52209e-014 | -1.53492e-013
| 2 | 35205.2 | 0.000309931 | -1436.06 | 472.036 | 0.000101875 | 1.53492e-013
9(Truss Beam- | 1 | -36869 | -0.000561031 | 391.901 | 180.165 | 0.000257918 | -2.31192e-013

Analyzed with SolidWorks Simulation | Simulation of Main Frame | 11
Trim[4]) | 2 | 36869 | 0.00345061 | -391.948 | 69.2249 | 0.000609439 | 2.31192e-013
Beam-10(Bottom miter 1[2]) | 1 | -33904.3 | 7.45638e-013 | -3422.2 | 1229.01 | -4.12376e-013 | -4.57497e-013
| 2 | 44139.8 | 0.0209319 | 989.398 | 372.071 | -0.0078716 | 4.76845e-012
| 3 | 33904.3 | -7.45639e-013 | 3422.2 | 1093.49 | 9.18409e-013 | 4.57497e-013

## Beam Stresses

Beam Name | Joints | Axial(N/m^2) | Bending Dir1(N/m^2) | Bending Dir2(N/m^2) | Torsional (N/m^2) | Worst Case(N/m^2)
Beam-1(Truss Trim[2]) | 1 | 6.55646e+007 | -4.78852e+007 | 118.748 | -4.37233e-009 | 1.1345e+008
| 2 | 6.55646e+007 | 5.61814e+007 | -96.0044 | 4.37236e-009 | 1.21746e+008
Beam-2(Bottom miter 2[2]) | 1 | 5.17101e+007 | -1.87295e+007 | -1.34825e-007 | 1.04953e-007 | 7.04395e+007
| 2 | 3.98139e+007 | 6.50206e+007 | -9.50619e-009 | -4.05061e-009 | 1.04835e+008
| 3 | 3.98139e+007 | -6.86925e+007 | 2.42967e-008 | 4.05061e-009 | 1.08506e+008
Beam-3(Bottom miter 2[1]) | 1 | 9.40051e+006 | -1.67665e-008 | -7.46369e+006 | 4.32304e-009 | 1.68642e+007
| 2 | 9.40051e+006 | -3.14317e-009 | 421267 | -4.44762e-009 | 9.82178e+006
| 3 | 2.25417e+007 | -2.56422e-009 | -2.9641e+007 | -1.17731e-009 | 5.21826e+007
| 4 | 9.156e+006 | 9.25554e-009 | -515953 | 1.44136e-008 | 9.67195e+006
Beam-4(Deck trim) | 1 | -1.91233e+006 | -7.29966e-008 | -1.74554e+007 | 4.53783e-008 | 1.93677e+007
| 2 | -1.91233e+006 | -1.10211e-007 | 3.18441e+007 | -4.53783e-008 | 3.37564e+007
| 3 | -1.90345e+007 | 7.64058e-008 | -4.88893e+006 | 1.53318e-008 | 2.39234e+007
| 4 | -1.92888e+007 | -6.59458e-010 | -9.58034e+007 | 3.43328e-008 | 1.15092e+008
| 5 | -1.80103e+006 | 1.18815e-007 | 3.76293e+007 | 1.24529e-008 | 3.94303e+007
Beam-5(Truss Trim[5]) | 1 | 6.63272e+007 | 4.54061e+007 | -304.948 | -2.10533e-009 | 1.11734e+008
| 2 | 0 | 0 | 0 | 0 | 0
Beam-6(Truss Trim[3]) | 1 | -6.58532e+007 | -2.31607e+007 | -125.624 | 5.85678e-009 | 8.9014e+007
| 2 | -6.58532e+007 | 9.46506e+006 | -33.8834 | -5.85664e-009 | 7.53183e+007
Beam-7(Truss Trim[1]) | 1 | -6.6134e+007 | 6.46178e+007 | -146.626 | -6.43101e-009 | 1.30752e+008
| 2 | -6.6134e+007 | -5.99641e+007 | 53.3592 | 6.43101e-009 | 1.26098e+008
Beam-8(Truss Trim[6]) | 1 | -6.4684e+007 | 5.94783e+007 | -4.70619e-009 | -8.17007e-009 | 1.24162e+008
| 2 | -6.4684e+007 | -6.30732e+007 | 13.6125 | 8.17006e-009 | 1.27757e+008
Beam-9(Truss Trim[4]) | 1 | -6.7741e+007 | 2.40736e+007 | -34.4629 | -1.23059e-008 | 9.18146e+007
| 2 | -6.7741e+007 | -9.24978e+006 | 81.4328 | 1.23059e-008 | 7.69908e+007
Beam-10(Bottom miter 1[2]) | 1 | 3.91124e+007 | -6.35441e+007 | -2.13213e-008 | -9.89751e-009 | 1.02656e+008
| 2 | 5.09201e+007 | 1.92373e+007 | 406.989 | 1.03161e-007 | 7.01579e+007
| 3 | 3.91124e+007 | 5.65371e+007 | -4.74849e-008 | 9.89751e-009 | 9.56495e+007

Analyzed with SolidWorks Simulation | Simulation of Main Frame | 12


Analyzed with SolidWorks Simulation | Simulation of Main Frame | 13

## Study Results

Name | Type | Min | Max
Stress1 | TXY: Shear in Y Dir. on YZ Plane | 0 ksi Element: 233 | 18.964 ksi Element: 164

Main Frame-Center Load-Stress-Stress1

Name | Type | Min | Max
Displacement1 | URES: Resultant Displacement | 0 in Node: 57 | 0.0482452 in Node: 104


Analyzed with SolidWorks Simulation | Simulation of Main Frame | 14

Main Frame-Center Load-Displacement-Displacement1

Name | Type
Displacement1{1} | URES: Resultant Displacement


Analyzed with SolidWorks Simulation | Simulation of Main Frame | 15

Main Frame-Center Load-Displacement-Displacement1{1}

Name | Type | Min | Max
Factor of Safety1 | Automatic | 1.68712 Node: 166 | 22.4597 Node: 17


Analyzed with SolidWorks Simulation | Simulation of Main Frame | 16

Main Frame-Center Load-Factor of Safety-Factor of Safety1

## Conclusion

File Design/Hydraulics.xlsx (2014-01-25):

Piston Bore | 4.00"
Piston area | 12.57"
PSI | 1500PSI
Force | 18849.55592lb
Pump Volume per sec | 0.7gpm | 0.8gpm | 1.6gpm
Pump Volume per sec | 2.7In³/sec | 3.1In³/sec | 6.2In³/sec
Piston speed | 0.21in/s | 0.25in/s | 0.49in/s
Time to move 4" | 18.7s | 16.3s | 8.2s
Pump RPM | 1200RPM | 1800RPM | 3600RPM
1280000

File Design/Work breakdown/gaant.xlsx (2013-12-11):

Week | 2014-01-13 | 2014-01-20 | 2014-01-27 | 2014-02-03 | 2014-02-10 | 2014-02-17 | 2014-02-24 | 2014-03-03 | 2014-03-10 | 2014-03-17 | 2014-03-24 | 2014-03-31 | 2014-04-07 | 2014-04-14 | 2014-04-21 | 2014-04-28 | 2014-05-05
Hydraulics
Spec parts | x | x
Purchase | x | x | x | x
Assemble |  |  | x | x | x | x | x | x
Attach to frame |  |  |  |  |  |  | x | x | x
Calibrate |  |  |  |  |  |  |  |  |  | x |  |  |  |  | x | x
Frame
Design | x | x
Purchase |  | x | x | x
Fabricate |  |  |  | x | x | x | x
Assemble |  |  |  |  |  | x | x | x | x
Raspberry Pi
Purchase | x
Install Raspbian OS |  | x
Program with Python |  |  | x | x | x | x
Interface |  |  |  | x | x | x | x | x | x | x
Attach to Frame |  |  |  |  |  |  |  |  |  |  | x | x | x | x

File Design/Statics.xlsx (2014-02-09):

 | Tubing
B | H | Wall | I Full | I | A | Span | Force | Deflection | M | Density | Weight | C | Yield | Max KSI | % strength
3 | 3 | 0.25 | 6.75 | 3.494791667 | 2.75 | 20" | 10000 lb | 0.0164" | 50000 |  | 0 | 1.5 | 21460.50671 | 36000 | 59.61%
3 | 3 | 0.125 | 6.75 | 1.984049479 | 1.4375 | 20" | 10000 lb | 0.0290" | 50000 |  | 0 | 1.5 | 37801.47662 | 36000 | 105.00%
3 | 3 | 0.08 | 6.75 | 1.328841387 | 0.9344 | 20" | 10000 lb | 0.0432" | 50000 |  | 0 | 1.5 | 56440.14459 | 36000 | 156.78%
3 | 3 | 0.06 | 6.75 | 1.01691072 | 0.7056 | 20" | 10000 lb | 0.0565" | 50000 |  | 0 | 1.5 | 73752.78727 | 36000 | 204.87%
3 | 3 | 0.032 | 6.75 | 0.5578287459 | 0.379904 | 20" | 10000 lb | 0.1030" | 50000 |  | 0 | 1.5 | 134449.8658 | 36000 | 373.47%
3 | 4 | 0.25 | 16 | 7.067708333 | 3.25 | 20" | 10000 lb | 0.0081" | 50000 |  | 0 | 2 | 14148.85777 | 36000 | 39.30%
3 | 4 | 0.125 | 16 | 3.915039062 | 1.6875 | 20" | 10000 lb | 0.0147" | 50000 |  | 0 | 2 | 25542.52931 | 36000 | 70.95%
3 | 4 | 0.08 | 16 | 2.59919872 | 1.0944 | 20" | 10000 lb | 0.0221" | 50000 |  | 0 | 2 | 38473.39537 | 36000 | 106.87%
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

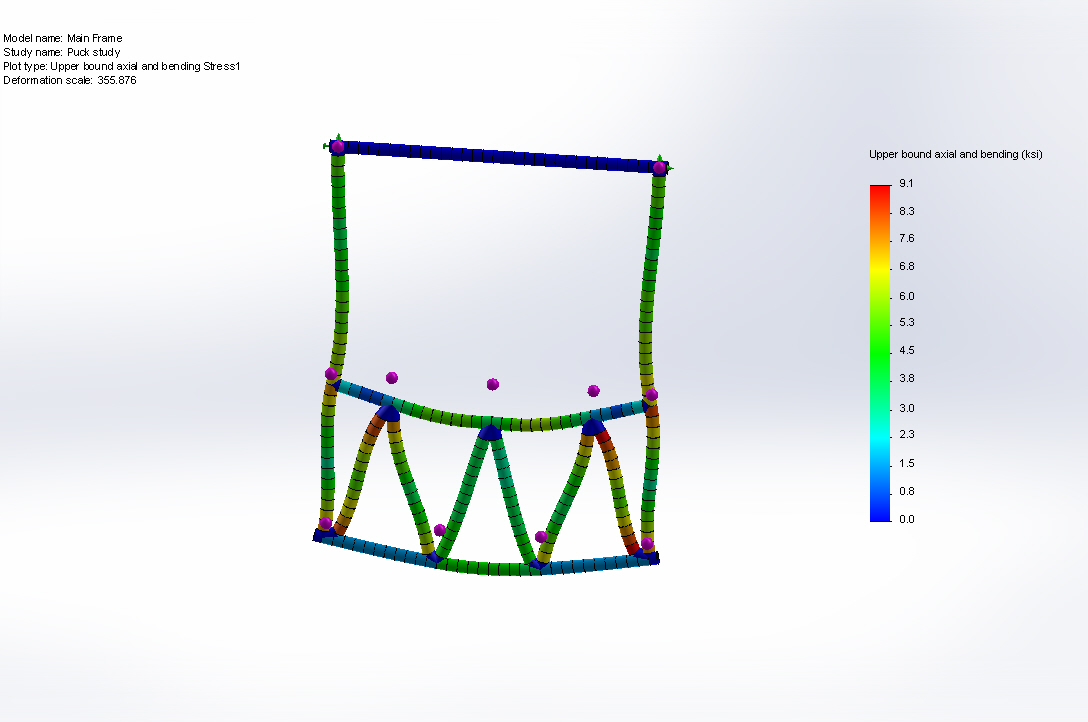
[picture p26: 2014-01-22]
Design/Solidworks Models/Frame REV 2_2/Main Frame-Puck study-Image-1.jpg

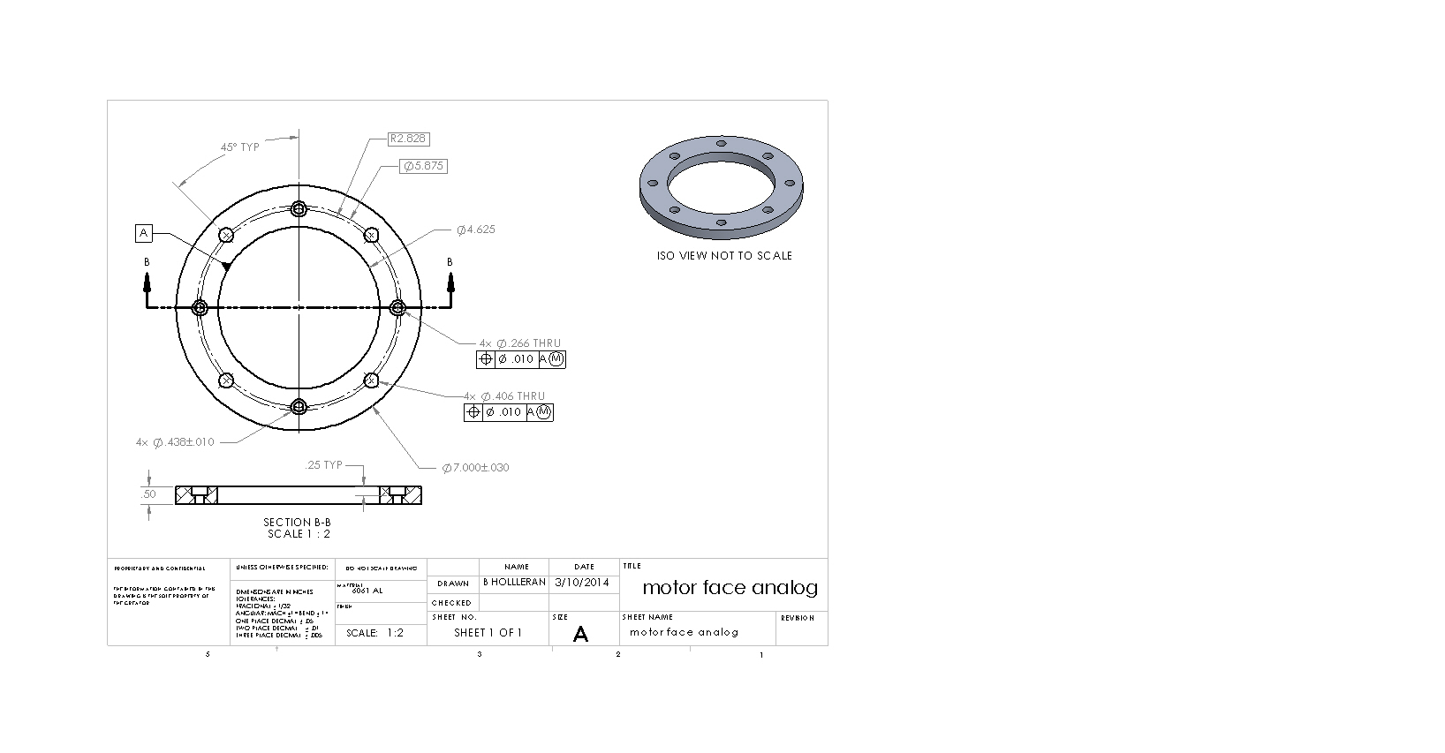
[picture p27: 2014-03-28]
Design/Solidworks Models/Frame Optimization REV 2/motor face analog.JPG

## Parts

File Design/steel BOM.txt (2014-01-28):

Vertical beams = 73.5" x2 1/8in thick 3x3 steel tubing

Horizontal beam = 57" 1/8in thick 3x6 steel tubing

trusses = 30" x6 1/8in thick 2x2 steel tubing

base feet = 30' x2 1/8in thick 3x3 steel tubing

bottom + top beams = 63" x2 1/8in thick 3x3 steel tubing

30 + 30 + 63 + 63 + 73.5 + 73.5 = 30' of 3x3in steel

57 3x6 = 5' of 3x6in steel

16' of 2x2in steel

30' of 2x2in steel for gussets and top truss

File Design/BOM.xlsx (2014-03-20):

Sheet: Main
 | Name | Orderer | Link | Qt | Price | Shipping | Total |  |  | Category | Total
 | Electronics |  |  |  |  |  |  | $630.52 |  | Electronics | $630.52
 | 7 segment display | Bob | http://www.digikey.com/product-detail/en/SA40-19EWA/754-1691-5-ND/3084503 | 5 | $16.46 | $15.00 | $97.30 |  |  | Hydraulics | $1681.22
 | Rasberry Pi | Bob | http://www.amazon.com/CanaKit-Raspberry-Basic-Clear-Supply/dp/B00DG9D6IK | 1 | $55.00 | $12.72 | $67.72 |  |  | Mechanical | $491.52
 | Monitor | Bob | http://www.amazon.com/Asus-VE228H-21-5-Inch-Integrated-Speakers/dp/B00413PHDM | 1 | $136.00 | $0.00 | $136.00 |  |  | Raw Materials | $545.27
 | hdmi cord | Bob | http://www.amazon.com/AmazonBasics-High-Speed-HDMI-Cable-Meters/dp/B003L1ZYYM | 1 | $5.79 | $0.00 | $5.79 |  |  | Total | $3348.53
 | i2c ADC | Bob | http://www.adafruit.com/products/1085 | 1 | $14.95 | $4.07 | $19.02
 | Switches | Bob | http://www.adafruit.com/products/1010 | 1 | $5.95 | $0.00 | $5.95
 | Misc | TBD |  | 1 | $150.00 | $0.00 | $150.00
 | USB external HDD | Bob | http://www.amazon.com/Protronix-External-Portable-Drive-Black/dp/B004CG1UCK?s=electronics | 1 | $28.00 | $7.49 | $35.49
 | 7-Seg I2C | Bob | http://www.adafruit.com/products/1427?gclid=CN_51IzmvbwCFcpZ7AodslYAPQ | 5 | $5.95 | $7.50 | $37.25
 | Wireless router | Bob | http://www.newegg.com/Product/Product.aspx?Item=N82E16833166072 | 1 | $30.00 | $0.00 | $30.00
 | Pi Breakout | Bob | http://www.adafruit.com/products/1105 | 1 | $8.00 | $0.00 | $8.00
 | I2C level shifter | Bob | http://www.abelectronics.co.uk/products/3/Raspberry-Pi/37/Buffer-Pi | 1 | $28.00 | $10.00 | $38.00
 |  |  |  |  |  |  | $0.00
 | Hydraulics |  |  |  |  |  |  | $1681.22
 | Pump | Geoff | http://www.grainger.com/product/HALDEX-BARNES-Pump-4F651?s_pp=false | 1 | $171.75 | $24.32 | $196.07
 | Motor | Geoff | http://www.automationdirect.com/adc/Shopping/Catalog/Motors/AC_Motors_-_General_Purpose_and_Inverter_Duty_(0.25_-_300HP)/AC_Motors-General_Purpose,_Rolled_Ste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 | 1 | $123.00 | $0.00 | $123.00
 | Cylinder | Geoff | http://www.grainger.com/product/MAXIM-Hydraulic-Cylinder-6FDA8?Pid=search | 1 | $236.50 | $0.00 | $236.50
 | Sensor (0-5V) | Geoff | http://www.instrumart.com/products/30859/ashcroft-a2-heavy-industrial-pressure-transmitter | 1 | $391.50 | $0.00 | $391.50
 | Lines | TBD | Tractor Supply | 5 | $100.00 | $0.00 | $500.00
 | Valve | Geoff | http://www.northerntool.com/shop/tools/product_472_472 | 1 | $85.00 | $0.00 | $85.00
 | Tank | Geoff | http://www.northerntool.com/shop/tools/product_200466862_200466862 | 1 | $70.00 | $0.00 | $70.00
 | Filter housing | Geoff | http://www.grainger.com/product/Spin-on-Filter-3KML8?s_pp=false | 1 | $40.00 | $0.00 | $40.00
 | Filter Cartridge | Geoff | http://www.grainger.com/product/PARKER-Filter-Element-1R412?opr=OAPD&pbi=3KML8 | 1 | $20.00 | $0.00 | $20.00
 |  |  |  |  |  | $0.00 | $0.00
 | Motor Coupling | Bob | http://www.amazonsupply.com/lovejoy-standard-coupling-sintered-through/dp/B003HIWOGA | 1 | $4.22 | $0.00 | $4.22
 | Pump Coupling | Bob | http://www.amazonsupply.com/s/ref=sp_search?guess=true&Action=submit&keywords=68514447952 | 1 | $5.29 | $0.00 | $5.29
 | Coupling Spider | Bob | http://www.amazonsupply.com/lovejoy-coupling-center-elastomer-spider/dp/B007SX3IO2 | 2 | $2.29 | $0.00 | $4.58
 | Motor Coupling | Bob | http://www.amazonsupply.com/dp/B003HIWOF6 | 1 | $5.06 | $0.00 | $5.06
 |  |  |  | 0 | $0.00 | $0.00 | $0.00
 |  |  |  |  |  |  | $0.00
 | Mechanical |  |  |  |  |  |  | $491.52 |  |  | Steel
 | Castors | Geoff | http://www.mcmaster.com/#22665t31/=qjbaja | 4 | $47.88 | $0.00 | $191.52 |  |  |  | Dimensional
 | Misc Hardware | TBD |  | 1 | $300.00 | $0.00 | $300.00 |  |  |  | 2x2x 1/8 | 3x3x 1/8 | 3x6x 3/16
 |  |  |  |  |  | $0.00 | $0.00 |  |  |  | 30.0 in | 32.0 in | 57.0 in
 |  |  |  |  |  | $0.00 | $0.00 |  |  |  | 30.0 in | 32.0 in | 4.0 in
 |  |  |  |  |  | $0.00 | $0.00 |  |  |  | 30.0 in | 65.0 in | 4.0 in
 |  |  |  |  |  | $0.00 | $0.00 |  |  |  | 30.0 in | 65.0 in | 4.0 in
 |  |  |  |  |  | $0.00 | $0.00 |  |  |  | 30.0 in | 73.5 in | 4.0 in
 |  |  |  |  |  | $0.00 | $0.00 |  |  |  | 30.0 in | 73.5 in
 |  |  |  |  |  | $0.00 | $0.00 |  |  |  | 8.0 in
 | Raw Materials |  |  |  |  |  |  | $545.27 |  |  | 8.0 in
 | Frame Steel | Mike | http://www.capitalsteel.net/ | 0 | $0.00 | $0.00 | $0.00 |  |  |  | 8.0 in
 | 2x2x 1/8 | Geoff |  | 23.00 ft | $2.33 | $0.00 | $53.67 |  |  |  | 8.0 in
 | 3x3x 1/8 | Geoff |  | 28.42 ft | $3.62 | $0.00 | $103.01 |  |  |  | 16.0 in
 | 3x6x 3/16 | Geoff |  | 6.08 ft | $12.06 | $0.00 | $73.38 |  |  |  | 16.0 in
i | Steel Cuts at Capitol |  |  | 6 | $10.00 | $0.00 | $60.00 |  |  |  | 16.0 in
 |  |  |  |  | $0.00 | $0.00 | $0.00 |  |  |  | 16.0 in
 |  |  |  |  | $0.00 | $0.00 | $0.00 |  |  |  | 23.00 ft | 28.42 ft | 6.08 ft
 | Paint | TBD |  | 10 | $7.00 | $0.00 | $70.00
 | Aluminum plate 1'x6'x.5" | Geoff | http://www.mcmaster.com/#9246k65/=qjbgg9 | 1 | $185.21 | $0.00 | $185.21 |  |  | 10 foot lengths |  | 2x2 total | 3x3 total | 3x6 total
 |  |  |  |  |  | $0.00 | $0.00 |  | cut1 | 8 | 2x2 | 25.00 | 32.00 | 8.00
 |  |  |  |  |  | $0.00 | $0.00 |  | cut2 | 8 | 2x2
 |  |  |  |  |  | $0.00 | $0.00 |  | cut3 | 9 | 2x2
 |  |  |  |  |  | $0.00 | $0.00 |  | cut4 | 9 | 3x3
 |  |  |  |  |  | $0.00 | $0.00 |  | cut5 | 9 | 3x3
 |  |  |  |  |  |  |  |  | cut6 | 7 | 3x3
 |  |  |  |  |  |  |  |  | cut7 | 7 | 3x3
 |  |  |  |  |  |  |  |  | cut8 | 8 | 3x6

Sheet: Bob
Name | Orderer | Link | Qt | Price | Shipping | Total
Electronics | 0 | 0 | 0 | 0 | 0 | 0
7 segment display | Bob | http://www.digikey.com/product-detail/en/SA40-19EWA/754-1691-5-ND/3084503 | 5 | 16.46 | 15 | 97.3
Rasberry Pi | Bob | http://www.amazon.com/CanaKit-Raspberry-Basic-Clear-Supply/dp/B00DG9D6IK | 1 | 55 | 12.72 | 67.72
Monitor | Bob | http://www.amazon.com/Asus-VE228H-21-5-Inch-Integrated-Speakers/dp/B00413PHDM | 1 | 136 | 0 | 136
hdmi cord | Bob | http://www.amazon.com/AmazonBasics-High-Speed-HDMI-Cable-Meters/dp/B003L1ZYYM | 1 | 5.79 | 0 | 5.79
i2c ADC | Bob | http://www.adafruit.com/products/1085 | 1 | 14.95 | 4.07 | 19.02
Switches | Bob | http://www.adafruit.com/products/1010 | 1 | 5.95 | 0 | 5.95
Misc | TBD | 0 | 1 | 150 | 0 | 150
#REF! | #REF! | #REF! | #REF! | #REF! | #REF! | #REF!
USB external HDD | Bob | http://www.amazon.com/Protronix-External-Portable-Drive-Black/dp/B004CG1UCK?s=electronics | 1 | 28 | 7.49 | 35.49
7-Seg I2C | Bob | http://www.adafruit.com/products/1427?gclid=CN_51IzmvbwCFcpZ7AodslYAPQ | 5 | 5.95 | 7.5 | 37.25
Wireless router | Bob | http://www.newegg.com/Product/Product.aspx?Item=N82E16833166072 | 1 | 30 | 0 | 30
Pi Breakout | Bob | http://www.adafruit.com/products/1105 | 1 | 8 | 0 | 8
I2C level shifter | Bob | http://www.abelectronics.co.uk/products/3/Raspberry-Pi/37/Buffer-Pi | 1 | 28 | 10 | 38
0 | 0 | 0 | 0 | 0 | 0 | 0
0 | 0 | 0 | 0 | 0 | 0 | 0
Hydraulics | 0 | 0 | 0 | 0 | 0 | 0
Pump | Geoff | http://www.grainger.com/product/HALDEX-BARNES-Pump-4F651?s_pp=false | 1 | 171.75 | 24.32 | 196.07
Motor | Geoff | http://www.automationdirect.com/adc/Shopping/Catalog/Motors/AC_Motors_-_General_Purpose_and_Inverter_Duty_(0.25_-_300HP)/AC_Motors-General_Purpose,_Rolled_Ste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 | 1 | 123 | 0 | 123
Cylinder | Geoff | http://www.grainger.com/product/MAXIM-Hydraulic-Cylinder-6FDA8?Pid=search | 1 | 236.5 | 0 | 236.5
Sensor (0-5V) | Geoff | http://www.instrumart.com/products/30859/ashcroft-a2-heavy-industrial-pressure-transmitter | 1 | 391.5 | 0 | 391.5
Lines | TBD | Tractor Supply | 5 | 100 | 0 | 500
Valve | Geoff | http://www.northerntool.com/shop/tools/product_472_472 | 1 | 85 | 0 | 85
Tank | Geoff | http://www.northerntool.com/shop/tools/product_200466862_200466862 | 1 | 70 | 0 | 70
Filter housing | Geoff | http://www.grainger.com/product/Spin-on-Filter-3KML8?s_pp=false | 1 | 40 | 0 | 40
Filter Cartridge | Geoff | http://www.grainger.com/product/PARKER-Filter-Element-1R412?opr=OAPD&pbi=3KML8 | 1 | 20 | 0 | 20
0 | 0 | 0 | 0 | 0 | 0 | 0
Motor Coupling | Bob | http://www.amazonsupply.com/lovejoy-standard-coupling-sintered-through/dp/B003HIWOGA | 1 | 4.22 | 0 | 4.22
Pump Coupling | Bob | http://www.amazonsupply.com/s/ref=sp_search?guess=true&Action=submit&keywords=68514447952 | 1 | 5.29 | 0 | 5.29
Coupling Spider | Bob | http://www.amazonsupply.com/lovejoy-coupling-center-elastomer-spider/dp/B007SX3IO2 | 2 | 2.29 | 0 | 4.58
0 | 0 | 0 | 0 | 0 | 0 | 0
0 | 0 | 0 | 0 | 0 | 0 | 0
Mechanical | 0 | 0 | 0 | 0 | 0 | 0
Castors | Geoff | http://www.mcmaster.com/#22665t31/=qjbaja | 4 | 47.88 | 0 | 191.52
Misc Hardware | TBD | 0 | 1 | 300 | 0 | 300
0 | 0 | 0 | 0 | 0 | 0 | 0
0 | 0 | 0 | 0 | 0 | 0 | 0
0 | 0 | 0 | 0 | 0 | 0 | 0
0 | 0 | 0 | 0 | 0 | 0 | 0
0 | 0 | 0 | 0 | 0 | 0 | 0
0 | 0 | 0 | 0 | 0 | 0 | 0
0 | 0 | 0 | 0 | 0 | 0 | 0
Raw Materials | 0 | 0 | 0 | 0 | 0 | 0
Frame Steel | Mike | http://www.capitalsteel.net/ | 0 | 0 | 0 | 0
2x2x 1/8 | Geoff | 0 | 23 | 2.333333333 | 0 | 53.66666667
3x3x 1/8 | Geoff | 0 | 28.41666667 | 3.625 | 0 | 103.0104167
3x6x 3/16 | Geoff | 0 | 6.083333333 | 12.0625 | 0 | 73.38020833
Steel Cuts at Capitol | 0 | 0 | 6 | 10 | 0 | 60
0 | 0 | 0 | 0 | 0 | 0 | 0
0 | 0 | 0 | 0 | 0 | 0 | 0
Paint | TBD | 0 | 10 | 7 | 0 | 70
Aluminum plate 1'x6'x.5" | Geoff | http://www.mcmaster.com/#9246k65/=qjbgg9 | 1 | 185.21 | 0 | 185.21
0 | 0 | 0 | 0 | 0 | 0 | 0
0 | 0 | 0 | 0 | 0 | 0 | 0
0 | 0 | 0 | 0 | 0 | 0 | 0
0 | 0 | 0 | 0 | 0 | 0 | 0
0 | 0 | 0 | 0 | 0 | 0 | 0
0 | 0 | 0 | 0 | 0 | 0 | 0
0 | 0 | 0 | 0 | 0 | 0 | 0
0 | 0 | 0 | 0 | 0 | 0 | 0
0 | 0 | 0 | 0 | 0 | 0 | 0
0 | 0 | 0 | 0 | 0 | 0 | 0
0 | 0 | 0 | 0 | 0 | 0 | 0
0 | 0 | 0 | 0 | 0 | 0 | 0
0 | 0 | 0 | 0 | 0 | 0 | 0
0 | 0 | 0 | 0 | 0 | 0 | 0
0 | 0 | 0 | 0 | 0 | 0 | 0
0 | 0 | 0 | 0 | 0 | 0 | 0
0 | 0 | 0 | 0 | 0 | 0 | 0
0 | 0 | 0 | 0 | 0 | 0 | 0
0 | 0 | 0 | 0 | 0 | 0 | 0
0 | 0 | 0 | 0 | 0 | 0 | 0
0 | 0 | 0 | 0 | 0 | 0 | 0
0 | 0 | 0 | 0 | 0 | 0 | 0
0 | 0 | 0 | 0 | 0 | 0 | 0
0 | 0 | 0 | 0 | 0 | 0 | 0
0 | 0 | 0 | 0 | 0 | 0 | 0
0 | 0 | 0 | 0 | 0 | 0 | 0
0 | 0 | 0 | 0 | 0 | 0 | 0
0 | 0 | 0 | 0 | 0 | 0 | 0
0 | 0 | 0 | 0 | 0 | 0 | 0
0 | 0 | 0 | 0 | 0 | 0 | 0
0 | 0 | 0 | 0 | 0 | 0 | 0
0 | 0 | 0 | 0 | 0 | 0 | 0
0 | 0 | 0 | 0 | 0 | 0 | 0
0 | 0 | 0 | 0 | 0 | 0 | 0
0 | 0 | 0 | 0 | 0 | 0 | 0
0 | 0 | 0 | 0 | 0 | 0 | 0
0 | 0 | 0 | 0 | 0 | 0 | 0
0 | 0 | 0 | 0 | 0 | 0 | 0
0 | 0 | 0 | 0 | 0 | 0 | 0
0 | 0 | 0 | 0 | 0 | 0 | 0
0 | 0 | 0 | 0 | 0 | 0 | 0
0 | 0 | 0 | 0 | 0 | 0 | 0
0 | 0 | 0 | 0 | 0 | 0 | 0
0 | 0 | 0 | 0 | 0 | 0 | 0
0 | 0 | 0 | 0 | 0 | 0 | 0
0 | 0 | 0 | 0 | 0 | 0 | 0
0 | 0 | 0 | 0 | 0 | 0 | 0
0 | 0 | 0 | 0 | 0 | 0 | 0
0 | 0 | 0 | 0 | 0 | 0 | 0
0 | 0 | 0 | 0 | 0 | 0 | 0
0 | 0 | 0 | 0 | 0 | 0 | 0
0 | 0 | 0 | 0 | 0 | 0 | 0
0 | 0 | 0 | 0 | 0 | 0 | 0
0 | 0 | 0 | 0 | 0 | 0 | 0
0 | 0 | 0 | 0 | 0 | 0 | 0
0 | 0 | 0 | 0 | 0 | 0 | 0
0 | 0 | 0 | 0 | 0 | 0 | 0
0 | 0 | 0 | 0 | 0 | 0 | 0
0 | 0 | 0 | 0 | 0 | 0 | 0
0 | 0 | 0 | 0 | 0 | 0 | 0
0 | 0 | 0 | 0 | 0 | 0 | 0
0 | 0 | 0 | 0 | 0 | 0 | 0
0 | 0 | 0 | 0 | 0 | 0 | 0
0 | 0 | 0 | 0 | 0 | 0 | 0
0 | 0 | 0 | 0 | 0 | 0 | 0
0 | 0 | 0 | 0 | 0 | 0 | 0
0 | 0 | 0 | 0 | 0 | 0 | 0
0 | 0 | 0 | 0 | 0 | 0 | 0
0 | 0 | 0 | 0 | 0 | 0 | 0
0 | 0 | 0 | 0 | 0 | 0 | 0
0 | 0 | 0 | 0 | 0 | 0 | 0
0 | 0 | 0 | 0 | 0 | 0 | 0
0 | 0 | 0 | 0 | 0 | 0 | 0
0 | 0 | 0 | 0 | 0 | 0 | 0
0 | 0 | 0 | 0 | 0 | 0 | 0
0 | 0 | 0 | 0 | 0 | 0 | 0
0 | 0 | 0 | 0 | 0 | 0 | 0
0 | 0 | 0 | 0 | 0 | 0 | 0
0 | 0 | 0 | 0 | 0 | 0 | 0
0 | 0 | 0 | 0 | 0 | 0 | 0
0 | 0 | 0 | 0 | 0 | 0 | 0
0 | 0 | 0 | 0 | 0 | 0 | 0
0 | 0 | 0 | 0 | 0 | 0 | 0
0 | 0 | 0 | 0 | 0 | 0 | 0
0 | 0 | 0 | 0 | 0 | 0 | 0
0 | 0 | 0 | 0 | 0 | 0 | 0

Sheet: Mike
0 | 0 | 0 | 0 | 0 | 0 | 0
Name | Orderer | Link | Qt | Price | Shipping | Total
Electronics | 0 | 0 | 0 | 0 | 0 | 0 | 630.52 | 0 | 0 | Electronics | 630.52 | 0 | 0
7 segment display | Bob | http://www.digikey.com/product-detail/en/SA40-19EWA/754-1691-5-ND/3084503 | 5 | 16.46 | 15 | 97.3 | 0 | 0 | 0 | Hydraulics | 1681.22 | 0 | 0 | Bob
Rasberry Pi | Bob | http://www.amazon.com/CanaKit-Raspberry-Basic-Clear-Supply/dp/B00DG9D6IK | 1 | 55 | 12.72 | 67.72 | 0 | 0 | 0 | Mechanical | 491.52 | 0 | 0 | Bob | Leave this filter alone
Monitor | Bob | http://www.amazon.com/Asus-VE228H-21-5-Inch-Integrated-Speakers/dp/B00413PHDM | 1 | 136 | 0 | 136 | 0 | 0 | 0 | Raw Materials | 545.2672917 | 0 | 0 | Bob
hdmi cord | Bob | http://www.amazon.com/AmazonBasics-High-Speed-HDMI-Cable-Meters/dp/B003L1ZYYM | 1 | 5.79 | 0 | 5.79 | 0 | 0 | 0 | Total | 3348.527292 | 0 | 0 | Bob
i2c ADC | Bob | http://www.adafruit.com/products/1085 | 1 | 14.95 | 4.07 | 19.02 | 0 | 0 | 0 | 0 | 0 | 0 | 0 | Bob
Switches | Bob | http://www.adafruit.com/products/1010 | 1 | 5.95 | 0 | 5.95 | 0 | 0 | 0 | 0 | 0 | 0 | 0 | Bob
Misc | TBD | 0 | 1 | 150 | 0 | 150 | 0 | 0 | 0 | 0 | 0 | 0 | 0
#REF! | #REF! | #REF! | #REF! | #REF! | #REF! | #REF! | #REF! | #REF! | #REF! | #REF! | #REF! | #REF! | #REF! | #REF!
USB external HDD | Bob | http://www.amazon.com/Protronix-External-Portable-Drive-Black/dp/B004CG1UCK?s=electronics | 1 | 28 | 7.49 | 35.49 | 0 | 0 | 0 | 0 | 0 | 0 | 0 | Bob
7-Seg I2C | Bob | http://www.adafruit.com/products/1427?gclid=CN_51IzmvbwCFcpZ7AodslYAPQ | 5 | 5.95 | 7.5 | 37.25 | 0 | 0 | 0 | 0 | 0 | 0 | 0 | Bob
0 | 0 | 0 | 0 | 0 | 0 | 0 | 0 | 0 | 0 | 0 | 0 | 0 | 0
0 | 0 | 0 | 0 | 0 | 0 | 0 | 0 | 0 | 0 | 0 | 0 | 0 | 0
Hydraulics | 0 | 0 | 0 | 0 | 0 | 0 | 1681.22 | 0 | 0 | 0 | 0 | 0 | 0
Pump | Geoff | http://www.grainger.com/product/HALDEX-BARNES-Pump-4F651?s_pp=false | 1 | 171.75 | 24.32 | 196.07 | 0 | 0 | 0 | 0 | 0 | 0 | 0 | Geoff
Motor | Geoff | http://www.automationdirect.com/adc/Shopping/Catalog/Motors/AC_Motors_-_General_Purpose_and_Inverter_Duty_(0.25_-_300HP)/AC_Motors-General_Purpose,_Rolled_Ste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 | 1 | 123 | 0 | 123 | 0 | 0 | 0 | 0 | 0 | 0 | 0 | Geoff
Cylinder | Geoff | http://www.grainger.com/product/MAXIM-Hydraulic-Cylinder-6FDA8?Pid=search | 1 | 236.5 | 0 | 236.5 | 0 | 0 | 0 | 0 | 0 | 0 | 0 | Geoff
Sensor (0-5V) | Geoff | http://www.instrumart.com/products/30859/ashcroft-a2-heavy-industrial-pressure-transmitter | 1 | 391.5 | 0 | 391.5 | 0 | 0 | 0 | 0 | 0 | 0 | 0 | Geoff
Valve | Geoff | http://www.northerntool.com/shop/tools/product_472_472 | 1 | 85 | 0 | 85 | 0 | 0 | 0 | 0 | 0 | 0 | 0 | Geoff
Tank | Geoff | http://www.northerntool.com/shop/tools/product_200466862_200466862 | 1 | 70 | 0 | 70 | 0 | 0 | 0 | 0 | 0 | 0 | 0 | Geoff
Filter housing | Geoff | http://www.grainger.com/product/Spin-on-Filter-3KML8?s_pp=false | 1 | 40 | 0 | 40 | 0 | 0 | 0 | 0 | 0 | 0 | 0 | Geoff
Filter Cartridge | Geoff | http://www.grainger.com/product/PARKER-Filter-Element-1R412?opr=OAPD&pbi=3KML8 | 1 | 20 | 0 | 20 | 0 | 0 | 0 | 0 | 0 | 0 | 0 | Geoff
Castors | Geoff | http://www.mcmaster.com/#22665t31/=qjbaja | 4 | $47.88 | $0.00 | $191.52
0 | 0 | 0 | 0 | $0.00 | $0.00 | $0.00 | 0 | 0 | 0 | 0 | 0 | 0 | 0
Frame Steel | Mike | http://www.capitalsteel.net/ | 0 | $0.00 | $0.00 | $0.00
2x2x 1/8 | Geoff | 0 | 23 | $2.33 | $0.00 | $53.67
3x3x 1/8 | Geoff | 0 | 28.41666667 | $3.62 | $0.00 | $103.01
0 | 0 | 0 | 0 | $0.00 | $0.00 | $0.00 | 0 | 0 | 0 | 0 | 0 | 0 | 0
0 | 0 | 0 | 0 | $0.00 | $0.00 | $0.00 | 0 | 0 | 0 | 0 | 0 | 0 | 0
Mechanical | 0 | 0 | 0 | $0.00 | $0.00 | $0.00 | 491.52 | 0 | 0 | 0 | Steel | 0 | 0
3x6x 3/16 | Geoff | 0 | 6.083333333 | $12.06 | $0.00 | $73.38
Aluminum plate 1'x6'x.5" | Geoff | http://www.mcmaster.com/#9246k65/=qjbgg9 | 1 | $185.21 | $0.00 | $185.21
0 | 0 | 0 | 0 | 0 | 0 | 0 | 0 | 0 | 0 | 0 | 30 | 32 | 57
0 | 0 | 0 | 0 | 0 | 0 | 0 | 0 | 0 | 0 | 0 | 30 | 32 | 4
0 | 0 | 0 | 0 | 0 | 0 | 0 | 0 | 0 | 0 | 0 | 30 | 65 | 4
0 | 0 | 0 | 0 | 0 | 0 | 0 | 0 | 0 | 0 | 0 | 30 | 65 | 4
0 | 0 | 0 | 0 | 0 | 0 | 0 | 0 | 0 | 0 | 0 | 30 | 73.5 | 4
0 | 0 | 0 | 0 | 0 | 0 | 0 | 0 | 0 | 0 | 0 | 30 | 73.5 | 0
0 | 0 | 0 | 0 | 0 | 0 | 0 | 0 | 0 | 0 | 0 | 8 | 0 | 0
Raw Materials | 0 | 0 | 0 | 0 | 0 | 0 | 545.2672917 | 0 | 0 | 0 | 8 | 0 | 0
Lines | TBD | Tractor Supply | 5 | 100 | 0 | 500 | 0 | 0 | 0 | 0 | 8 | 0 | 0 | TBD
Motor Coupling | Bob | http://www.amazonsupply.com/lovejoy-standard-coupling-sintered-through/dp/B003HIWOGA | 1 | 4.22 | 0 | 4.22 | 0 | 0 | 0 | 0 | 8 | 0 | 0 | Bob
Pump Coupling | Bob | http://www.amazonsupply.com/s/ref=sp_search?guess=true&Action=submit&keywords=68514447952 | 1 | 5.29 | 0 | 5.29 | 0 | 0 | 0 | 0 | 16 | 0 | 0 | Bob
Coupling Spider | Bob | http://www.amazonsupply.com/lovejoy-coupling-center-elastomer-spider/dp/B007SX3IO2 | 2 | 2.29 | 0 | 4.58 | 0 | 0 | 0 | 0 | 16 | 0 | 0 | Bob
Steel Cuts at Capitol | 0 | 0 | 6 | 10 | 0 | 60 | 0 | 0 | 0 | 0 | 16 | 0 | 0
0 | 0 | 0 | 0 | 0 | 0 | 0 | 0 | 0 | 0 | 0 | 16 | 0 | 0
0 | 0 | 0 | 0 | 0 | 0 | 0 | 0 | 0 | 0 | 0 | 23 | 28.41666667 | 6.083333333
Misc Hardware | TBD | 0 | 1 | 300 | 0 | 300 | 0 | 0 | 0 | 0 | 0 | 0 | 0 | TBD
Paint | TBD | 0 | 10 | 7 | 0 | 70 | 0 | 0 | 0 | 10 foot lengths | 0 | 2x2 total | 3x3 total | TBD
0 | 0 | 0 | 0 | 0 | 0 | 0 | 0 | 0 | cut1 | 8 | 2x2 | 25 | 32
0 | 0 | 0 | 0 | 0 | 0 | 0 | 0 | 0 | cut2 | 8 | 2x2 | 0 | 0
0 | 0 | 0 | 0 | 0 | 0 | 0 | 0 | 0 | cut3 | 9 | 2x2 | 0 | 0
0 | 0 | 0 | 0 | 0 | 0 | 0 | 0 | 0 | cut4 | 9 | 3x3 | 0 | 0
0 | 0 | 0 | 0 | 0 | 0 | 0 | 0 | 0 | cut5 | 9 | 3x3 | 0 | 0
0 | 0 | 0 | 0 | 0 | 0 | 0 | 0 | 0 | cut6 | 7 | 3x3 | 0 | 0
0 | 0 | 0 | 0 | 0 | 0 | 0 | 0 | 0 | cut7 | 7 | 3x3 | 0 | 0
0 | 0 | 0 | 0 | 0 | 0 | 0 | 0 | 0 | cut8 | 8 | 3x6 | 0 | 0
0 | 0 | 0 | 0 | 0 | 0 | 0 | 0 | 0 | #REF! | #REF! | #REF! | 0 | 0
0 | 0 | 0 | 0 | 0 | 0 | 0 | 0 | 0 | #REF! | #REF! | #REF! | 0 | 0
0 | 0 | 0 | 0 | 0 | 0 | 0 | 0 | 0 | 0 | 0 | 0 | 0 | 0
0 | 0 | 0 | 0 | 0 | 0 | 0 | 0 | 0 | 0 | 0 | 0 | 0 | 0
0 | 0 | 0 | 0 | 0 | 0 | 0 | 0 | 0 | 0 | 0 | 0 | 0 | 0
0 | 0 | 0 | 0 | 0 | 0 | 0 | 0 | 0 | 0 | 0 | 0 | 0 | 0
0 | 0 | 0 | 0 | 0 | 0 | 0 | 0 | 0 | 0 | 0 | 0 | 0 | 0
0 | 0 | 0 | 0 | 0 | 0 | 0 | 0 | 0 | 0 | 0 | 0 | 0 | 0
0 | 0 | 0 | 0 | 0 | 0 | 0 | 0 | 0 | 0 | 0 | 0 | 0 | 0
0 | 0 | 0 | 0 | 0 | 0 | 0 | 0 | 0 | 0 | 0 | 0 | 0 | 0
0 | 0 | 0 | 0 | 0 | 0 | 0 | 0 | 0 | 0 | 0 | 0 | 0 | 0
0 | 0 | 0 | 0 | 0 | 0 | 0 | 0 | 0 | 0 | 0 | 0 | 0 | 0
0 | 0 | 0 | 0 | 0 | 0 | 0 | 0 | 0 | 0 | 0 | 0 | 0 | 0
0 | 0 | 0 | 0 | 0 | 0 | 0 | 0 | 0 | 0 | 0 | 0 | 0 | 0
0 | 0 | 0 | 0 | 0 | 0 | 0 | 0 | 0 | 0 | 0 | 0 | 0 | 0
0 | 0 | 0 | 0 | 0 | 0 | 0 | 0 | 0 | 0 | 0 | 0 | 0 | 0
0 | 0 | 0 | 0 | 0 | 0 | 0 | 0 | 0 | 0 | 0 | 0 | 0 | 0
0 | 0 | 0 | 0 | 0 | 0 | 0 | 0 | 0 | 0 | 0 | 0 | 0 | 0
0 | 0 | 0 | 0 | 0 | 0 | 0 | 0 | 0 | 0 | 0 | 0 | 0 | 0
0 | 0 | 0 | 0 | 0 | 0 | 0 | 0 | 0 | 0 | 0 | 0 | 0 | 0
0 | 0 | 0 | 0 | 0 | 0 | 0 | 0 | 0 | 0 | 0 | 0 | 0 | 0
0 | 0 | 0 | 0 | 0 | 0 | 0 | 0 | 0 | 0 | 0 | 0 | 0 | 0
0 | 0 | 0 | 0 | 0 | 0 | 0 | 0 | 0 | 0 | 0 | 0 | 0 | 0
0 | 0 | 0 | 0 | 0 | 0 | 0 | 0 | 0 | 0 | 0 | 0 | 0 | 0
0 | 0 | 0 | 0 | 0 | 0 | 0 | 0 | 0 | 0 | 0 | 0 | 0 | 0
0 | 0 | 0 | 0 | 0 | 0 | 0 | 0 | 0 | 0 | 0 | 0 | 0 | 0
0 | 0 | 0 | 0 | 0 | 0 | 0 | 0 | 0 | 0 | 0 | 0 | 0 | 0
0 | 0 | 0 | 0 | 0 | 0 | 0 | 0 | 0 | 0 | 0 | 0 | 0 | 0
0 | 0 | 0 | 0 | 0 | 0 | 0 | 0 | 0 | 0 | 0 | 0 | 0 | 0
0 | 0 | 0 | 0 | 0 | 0 | 0 | 0 | 0 | 0 | 0 | 0 | 0 | 0
0 | 0 | 0 | 0 | 0 | 0 | 0 | 0 | 0 | 0 | 0 | 0 | 0 | 0
0 | 0 | 0 | 0 | 0 | 0 | 0 | 0 | 0 | 0 | 0 | 0 | 0 | 0
0 | 0 | 0 | 0 | 0 | 0 | 0 | 0 | 0 | 0 | 0 | 0 | 0 | 0
0 | 0 | 0 | 0 | 0 | 0 | 0 | 0 | 0 | 0 | 0 | 0 | 0 | 0
0 | 0 | 0 | 0 | 0 | 0 | 0 | 0 | 0 | 0 | 0 | 0 | 0 | 0
0 | 0 | 0 | 0 | 0 | 0 | 0 | 0 | 0 | 0 | 0 | 0 | 0 | 0
0 | 0 | 0 | 0 | 0 | 0 | 0 | 0 | 0 | 0 | 0 | 0 | 0 | 0
0 | 0 | 0 | 0 | 0 | 0 | 0 | 0 | 0 | 0 | 0 | 0 | 0 | 0
0 | 0 | 0 | 0 | 0 | 0 | 0 | 0 | 0 | 0 | 0 | 0 | 0 | 0
0 | 0 | 0 | 0 | 0 | 0 | 0 | 0 | 0 | 0 | 0 | 0 | 0 | 0
0 | 0 | 0 | 0 | 0 | 0 | 0 | 0 | 0 | 0 | 0 | 0 | 0 | 0
0 | 0 | 0 | 0 | 0 | 0 | 0 | 0 | 0 | 0 | 0 | 0 | 0 | 0
0 | 0 | 0 | 0 | 0 | 0 | 0 | 0 | 0 | 0 | 0 | 0 | 0 | 0
0 | 0 | 0 | 0 | 0 | 0 | 0 | 0 | 0 | 0 | 0 | 0 | 0 | 0
0 | 0 | 0 | 0 | 0 | 0 | 0 | 0 | 0 | 0 | 0 | 0 | 0 | 0
0 | 0 | 0 | 0 | 0 | 0 | 0 | 0 | 0 | 0 | 0 | 0 | 0 | 0
0 | 0 | 0 | 0 | 0 | 0 | 0 | 0 | 0 | 0 | 0 | 0 | 0 | 0
0 | 0 | 0 | 0 | 0 | 0 | 0 | 0 | 0 | 0 | 0 | 0 | 0 | 0
0 | 0 | 0 | 0 | 0 | 0 | 0 | 0 | 0 | 0 | 0 | 0 | 0 | 0
0 | 0 | 0 | 0 | 0 | 0 | 0 | 0 | 0 | 0 | 0 | 0 | 0 | 0
0 | 0 | 0 | 0 | 0 | 0 | 0 | 0 | 0 | 0 | 0 | 0 | 0 | 0
0 | 0 | 0 | 0 | 0 | 0 | 0 | 0 | 0 | 0 | 0 | 0 | 0 | 0
0 | 0 | 0 | 0 | 0 | 0 | 0 | 0 | 0 | 0 | 0 | 0 | 0 | 0
0 | 0 | 0 | 0 | 0 | 0 | 0 | 0 | 0 | 0 | 0 | 0 | 0 | 0
0 | 0 | 0 | 0 | 0 | 0 | 0 | 0 | 0 | 0 | 0 | 0 | 0 | 0
0 | 0 | 0 | 0 | 0 | 0 | 0 | 0 | 0 | 0 | 0 | 0 | 0 | 0
0 | 0 | 0 | 0 | 0 | 0 | 0 | 0 | 0 | 0 | 0 | 0 | 0 | 0
0 | 0 | 0 | 0 | 0 | 0 | 0 | 0 | 0 | 0 | 0 | 0 | 0 | 0
0 | 0 | 0 | 0 | 0 | 0 | 0 | 0 | 0 | 0 | 0 | 0 | 0 | 0
0 | 0 | 0 | 0 | 0 | 0 | 0 | 0 | 0 | 0 | 0 | 0 | 0 | 0
0 | 0 | 0 | 0 | 0 | 0 | 0 | 0 | 0 | 0 | 0 | 0 | 0 | 0
0 | 0 | 0 | 0 | 0 | 0 | 0 | 0 | 0 | 0 | 0 | 0 | 0 | 0
0 | 0 | 0 | 0 | 0 | 0 | 0 | 0 | 0 | 0 | 0 | 0 | 0 | 0
0 | 0 | 0 | 0 | 0 | 0 | 0 | 0 | 0 | 0 | 0 | 0 | 0 | 0
0 | 0 | 0 | 0 | 0 | 0 | 0 | 0 | 0 | 0 | 0 | 0 | 0 | 0
0 | 0 | 0 | 0 | 0 | 0 | 0 | 0 | 0 | 0 | 0 | 0 | 0 | 0
0 | 0 | 0 | 0 | 0 | 0 | 0 | 0 | 0 | 0 | 0 | 0 | 0 | 0
0 | 0 | 0 | 0 | 0 | 0 | 0 | 0 | 0 | 0 | 0 | 0 | 0 | 0
0 | 0 | 0 | 0 | 0 | 0 | 0 | 0 | 0 | 0 | 0 | 0 | 0 | 0
0 | 0 | 0 | 0 | 0 | 0 | 0 | 0 | 0 | 0 | 0 | 0 | 0 | 0
0 | 0 | 0 | 0 | 0 | 0 | 0 | 0 | 0 | 0 | 0 | 0 | 0 | 0
0 | 0 | 0 | 0 | 0 | 0 | 0 | 0 | 0 | 0 | 0 | 0 | 0 | 0
0 | 0 | 0 | 0 | 0 | 0 | 0 | 0 | 0 | 0 | 0 | 0 | 0 | 0
0 | 0 | 0 | 0 | 0 | 0 | 0 | 0 | 0 | 0 | 0 | 0 | 0 | 0
0 | 0 | 0 | 0 | 0 | 0 | 0 | 0 | 0 | 0 | 0 | 0 | 0 | 0
0 | 0 | 0 | 0 | 0 | 0 | 0 | 0 | 0 | 0 | 0 | 0 | 0 | 0
0 | 0 | 0 | 0 | 0 | 0 | 0 | 0 | 0 | 0 | 0 | 0 | 0 | 0
0 | 0 | 0 | 0 | 0 | 0 | 0 | 0 | 0 | 0 | 0 | 0 | 0 | 0
0 | 0 | 0 | 0 | 0 | 0 | 0 | 0 | 0 | 0 | 0 | 0 | 0 | 0
0 | 0 | 0 | 0 | 0 | 0 | 0 | 0 | 0 | 0 | 0 | 0 | 0 | 0
0 | 0 | 0 | 0 | 0 | 0 | 0 | 0 | 0 | 0 | 0 | 0 | 0 | 0
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

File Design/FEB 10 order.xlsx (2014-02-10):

Name | Orderer | Link | Qt | Price | Shipping | Total
7 segment display | Bob | http://www.digikey.com/product-detail/en/SA40-19EWA/754-1691-5-ND/3084503 | 5 | $16.46 | $15.00 | $97.30
Rasberry Pi | Bob | http://www.amazon.com/CanaKit-Raspberry-Basic-Clear-Supply/dp/B00DG9D6IK | 1 | $55.00 | $12.72 | $67.72
USB external HDD | Bob | http://www.amazon.com/Protronix-External-Portable-Drive-Black/dp/B004CG1UCK?s=electronics | 1 | $28.00 | $7.49 | $35.49
7-Seg I2C | Bob | http://www.adafruit.com/products/1427?gclid=CN_51IzmvbwCFcpZ7AodslYAPQ | 5 | $5.95 | $7.50 | $37.25
Pi Breakout | Bob | http://www.adafruit.com/products/1105 | 1 | $8.00 | $4.50 | $12.50
GPIO buffer board | Bob | http://www.abelectronics.co.uk/products/3/Raspberry-Pi/37/Buffer-Pi | 1 | $28.00 | $10.00 | $38.00
 |  |  |  |  | Sum | $288.26

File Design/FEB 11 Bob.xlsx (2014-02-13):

Name | Link | Qt | Price | Shipping | Total
7 segment display | http://www.digikey.com/product-detail/en/SA40-19EWA/754-1691-5-ND/3084503 | 5 | $16.46 | $15.00 | $97.30
Rasberry Pi | http://www.amazon.com/CanaKit-Raspberry-Basic-Clear-Supply/dp/B00DG9D6IK | 1 | $55.00 | $12.72 | $67.72
Monitor | http://www.amazon.com/Asus-VE228H-21-5-Inch-Integrated-Speakers/dp/B00413PHDM | 1 | $136.00 | $0.00 | $136.00
hdmi cord | http://www.amazon.com/AmazonBasics-High-Speed-HDMI-Cable-Meters/dp/B003L1ZYYM | 1 | $5.79 | $0.00 | $5.79
Switches | http://www.adafruit.com/products/1010 | 1 | $5.95 | $0.00 | $5.95
USB external HDD | http://www.amazon.com/Protronix-External-Portable-Drive-Black/dp/B004CG1UCK?s=electronics | 1 | $28.00 | $7.49 | $35.49
7-Seg I2C | http://www.adafruit.com/products/1427?gclid=CN_51IzmvbwCFcpZ7AodslYAPQ | 5 | $5.95 | $7.50 | $37.25
Wireless router | http://www.newegg.com/Product/Product.aspx?Item=N82E16833166072 | 1 | $30.00 | $0.00 | $30.00
Pi Breakout | http://www.adafruit.com/products/1105 | 1 | $8.00 | $0.00 | $8.00
GPIO buffer board | http://www.abelectronics.co.uk/products/3/Raspberry-Pi/37/Buffer-Pi | 1 | $28.00 | $10.00 | $38.00
Motor Coupling | http://www.amazonsupply.com/lovejoy-standard-coupling-sintered-through/dp/B003HIWOGA | 1 | $4.22 | $0.00 | $4.22
Pump Coupling | http://www.amazonsupply.com/s/ref=sp_search?guess=true&Action=submit&keywords=68514447952 | 1 | $5.29 | $0.00 | $5.29
Coupling Spider | http://www.amazonsupply.com/lovejoy-coupling-center-elastomer-spider/dp/B007SX3IO2 | 2 | $2.29 | $0.00 | $4.58
 |  |  |  | Total | $475.59

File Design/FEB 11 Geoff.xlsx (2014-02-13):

Name | Link | Qt | Price | Shipping | Total
Pump | http://www.grainger.com/product/HALDEX-BARNES-Pump-4F651?s_pp=false | 1 | $171.75 | $24.32 | $196.07
Motor | http://www.automationdirect.com/adc/Shopping/Catalog/Motors/AC_Motors_-_General_Purpose_and_Inverter_Duty_(0.25_-_300HP)/AC_Motors-General_Purpose,_Rolled_Ste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 | 1 | $123.00 | $0.00 | $123.00
Cylinder | http://www.grainger.com/product/MAXIM-Hydraulic-Cylinder-6FDA8?Pid=search | 1 | $236.50 | $0.00 | $236.50
Sensor (0-5V) | http://www.instrumart.com/products/30859/ashcroft-a2-heavy-industrial-pressure-transmitter | 1 | $391.50 | $0.00 | $391.50
Valve | http://www.northerntool.com/shop/tools/product_472_472 | 1 | $85.00 | $0.00 | $85.00
Tank | http://www.northerntool.com/shop/tools/product_200466862_200466862 | 1 | $70.00 | $0.00 | $70.00
Filter housing | http://www.grainger.com/product/Spin-on-Filter-3KML8?s_pp=false | 1 | $40.00 | $0.00 | $40.00
Filter Cartridge | http://www.grainger.com/product/PARKER-Filter-Element-1R412?opr=OAPD&pbi=3KML8 | 1 | $20.00 | $0.00 | $20.00
Castors | http://www.mcmaster.com/#22665t31/=qjbaja | 4 | $47.88 | $0.00 | $191.52
Aluminum plate 1'x6'x.5" | http://www.mcmaster.com/#9246k65/=qjbgg9 | 1 | $185.21 | $0.00 | $185.21
 |  |  |  |  | $0.00
 |  |  |  |  | $0.00
 |  |  |  |  | $0.00
 |  |  |  |  | $0.00
 |  |  |  | Total | $1538.80

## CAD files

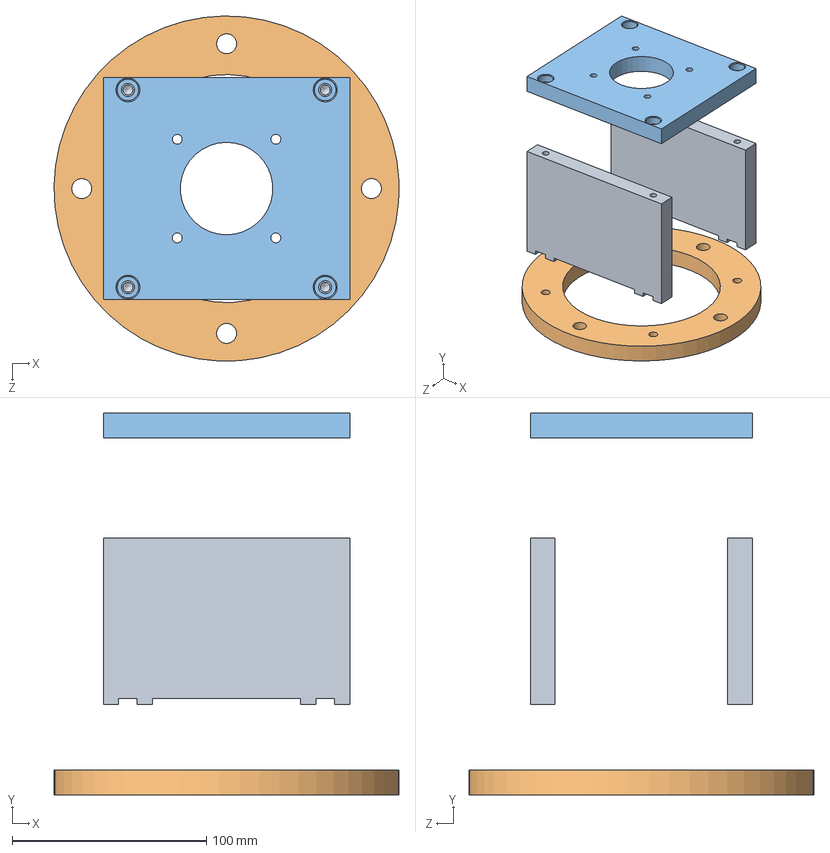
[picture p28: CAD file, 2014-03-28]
Design/Solidworks Models/Frame Optimization REV 2/bracket assembly.SLDASM
177.7 x 196.6 x 177.7 mm
motor standoff x 2
motor face analog
pump face bracket

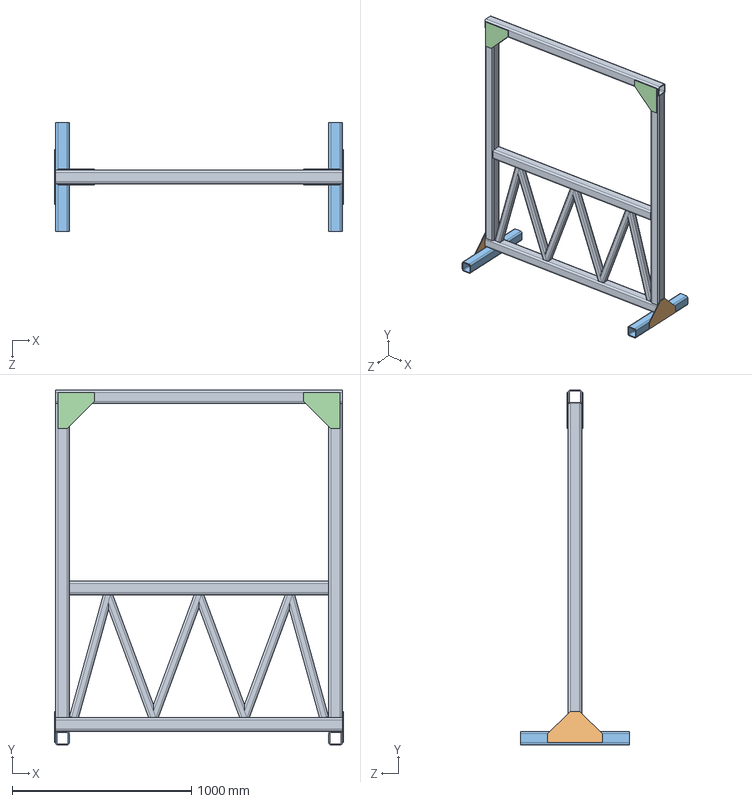
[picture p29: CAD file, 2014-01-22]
Design/Solidworks Models/Frame REV 2_2/Frame Assembled.SLDASM
1612.9 x 1981.2 x 609.6 mm
Main Frame
Foot side gussetts x 2
2ft foot beam x 2
Top gussetts x 4

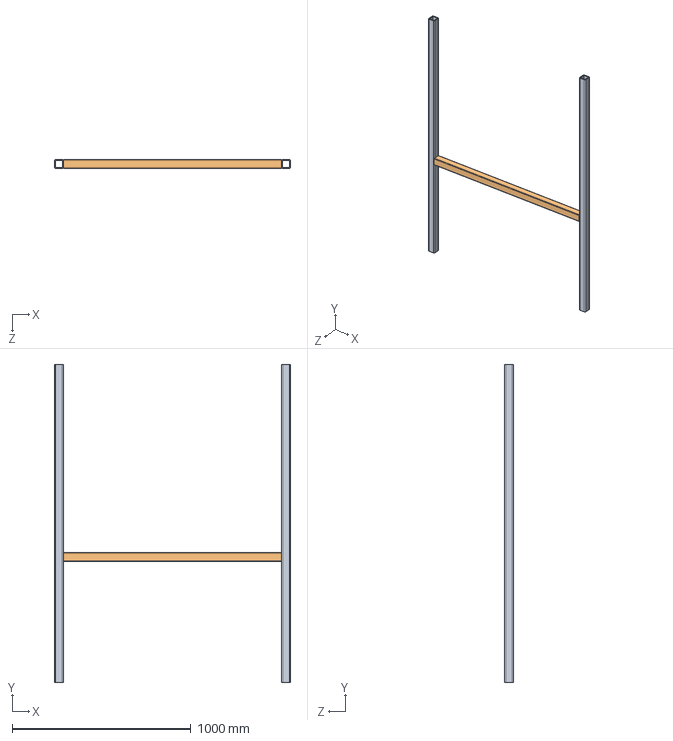
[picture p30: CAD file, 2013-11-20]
Design/Prototype & Testing/Truss/Top Truss.SLDASM
1320.8 x 1778.0 x 50.8 mm
Vertical x 2
Deck

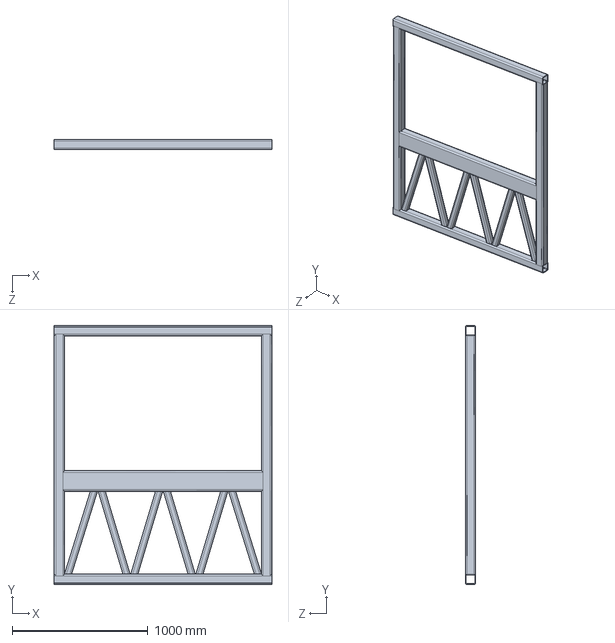
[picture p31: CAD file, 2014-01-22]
Design/Solidworks Models/Frame REV 2_2/Main Frame.SLDPRT
1600.2 x 1905.0 x 76.2 mm

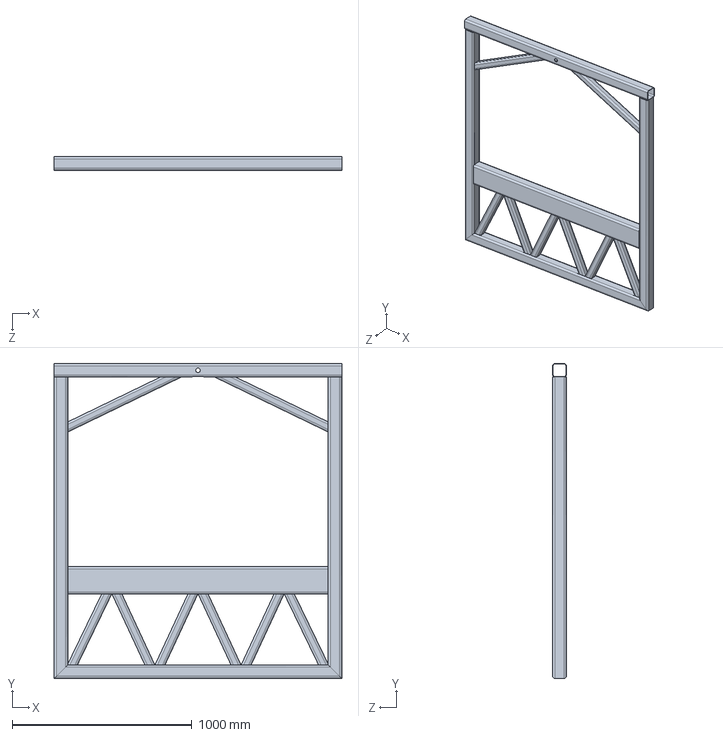
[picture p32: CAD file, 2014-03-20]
Design/Solidworks Models/Frame Optimization REV 2/Main Frame.SLDPRT
1600.2 x 1752.6 x 76.2 mm

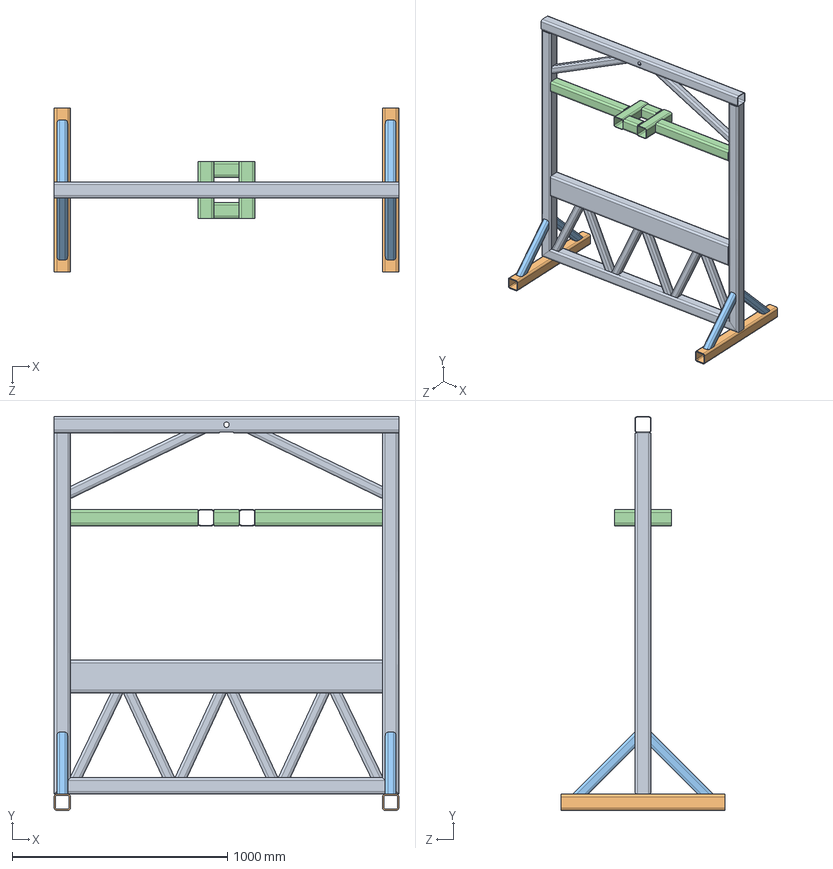
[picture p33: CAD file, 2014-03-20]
Design/Solidworks Models/Frame Optimization REV 2/Frame Assembled with top.SLDASM
1600.2 x 1828.8 x 762.0 mm
Main Frame
2ft foot beam x 2
2x2 foot gussetts x 4
Crossbeam 2.0

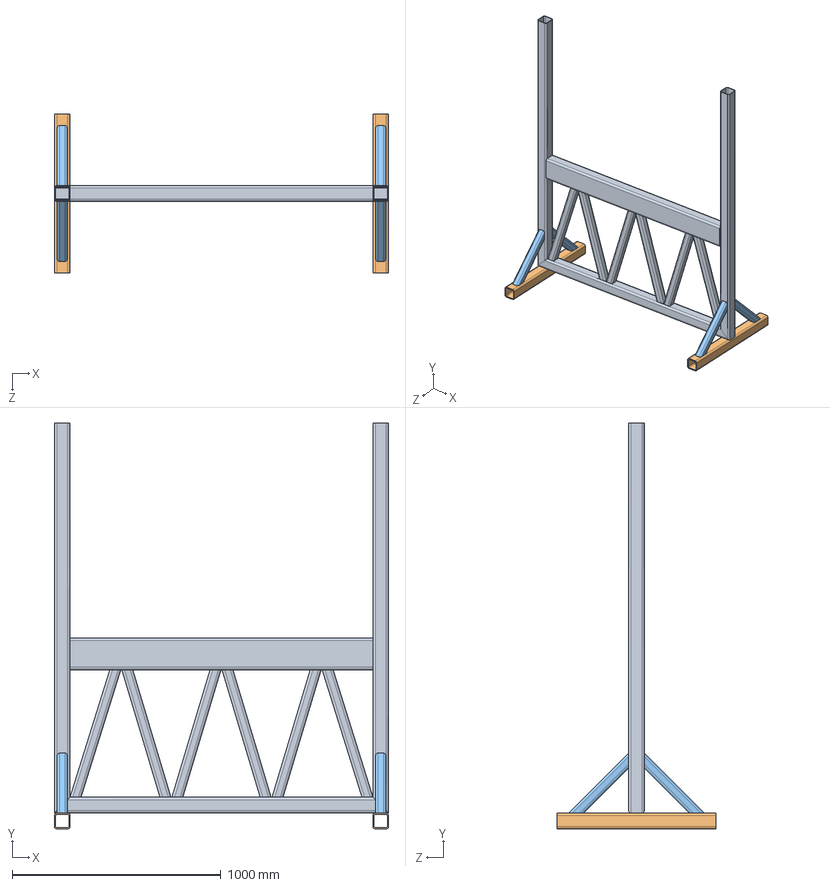
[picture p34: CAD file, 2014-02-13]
Design/Solidworks Models/Frame Optimization REV 2/Frame Assembled.SLDASM
1600.2 x 1943.1 x 762.0 mm
Main Frame
2ft foot beam x 2
2x2 foot gussetts x 4

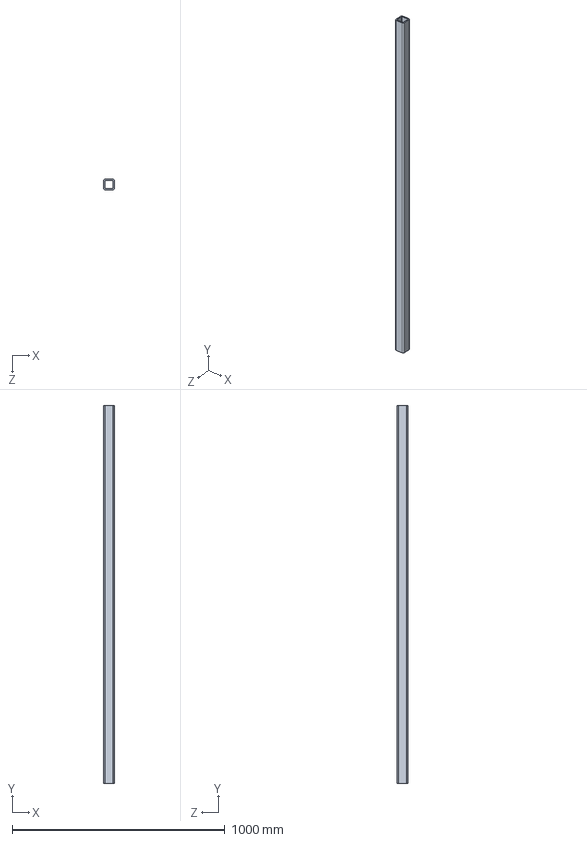
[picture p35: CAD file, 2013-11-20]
Design/Prototype & Testing/Truss/Vertical.SLDPRT
50.8 x 1778.0 x 50.8 mm

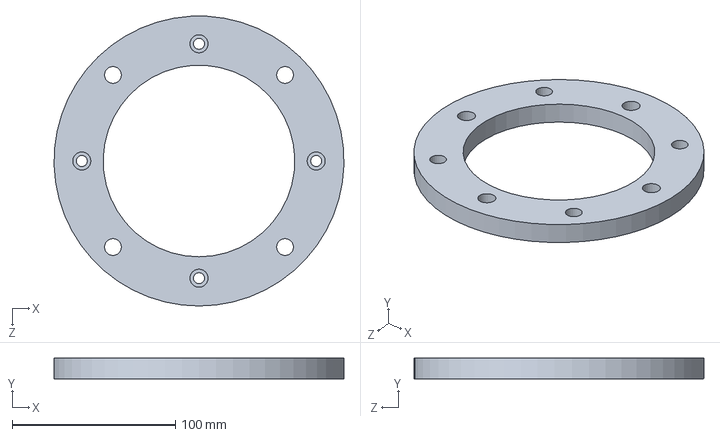
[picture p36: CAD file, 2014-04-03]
Design/Solidworks Models/Frame Optimization REV 2/motor face analog.SLDPRT
177.7 x 12.7 x 177.8 mm

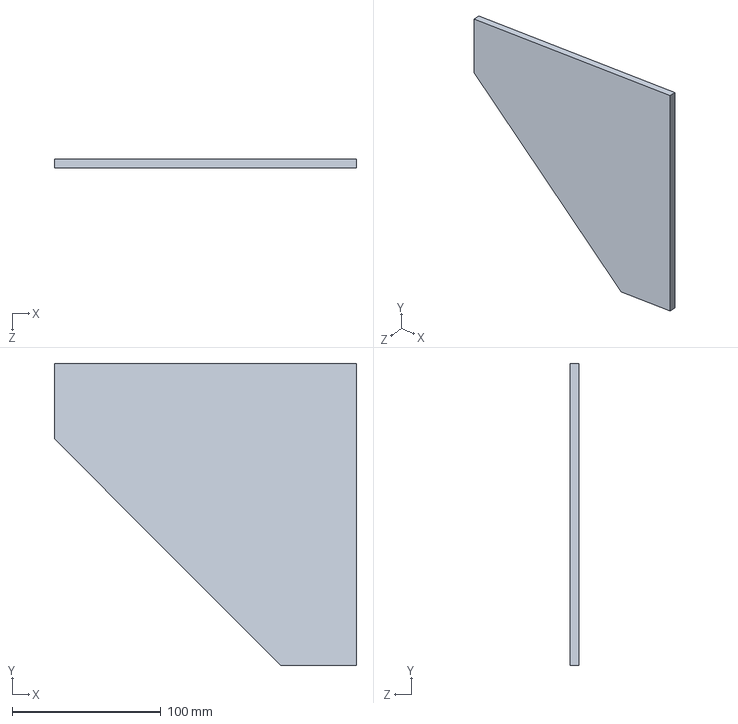
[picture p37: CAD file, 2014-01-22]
Design/Solidworks Models/Frame REV 2_2/Top gussetts.SLDPRT
203.2 x 203.2 x 6.35 mm

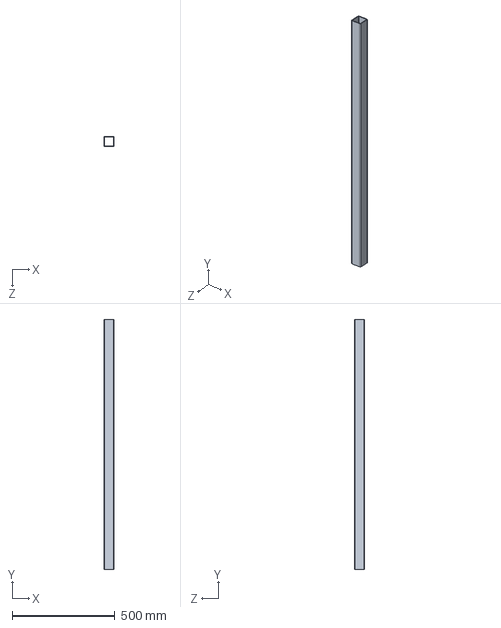
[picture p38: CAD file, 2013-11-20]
Design/Prototype & Testing/Truss/Deck.SLDPRT
50.8 x 1219.2 x 50.8 mm

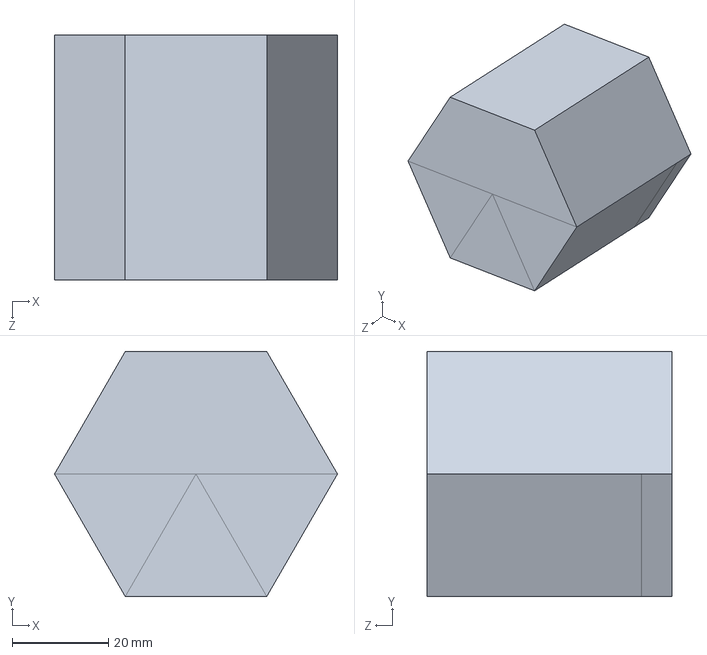
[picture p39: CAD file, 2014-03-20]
Design/Solidworks Models/Frame Optimization REV 2/Part1.SLDPRT
58.7 x 50.8 x 50.8 mm

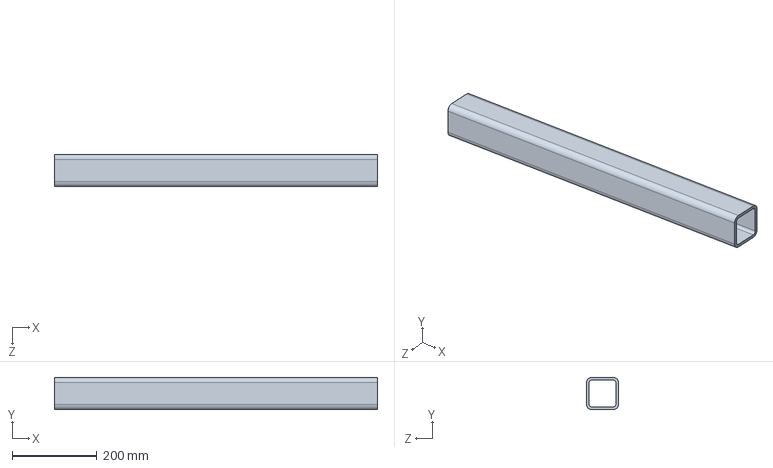
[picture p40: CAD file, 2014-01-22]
Design/Solidworks Models/Frame REV 2_2/2ft foot beam.SLDPRT
762.0 x 76.2 x 76.2 mm

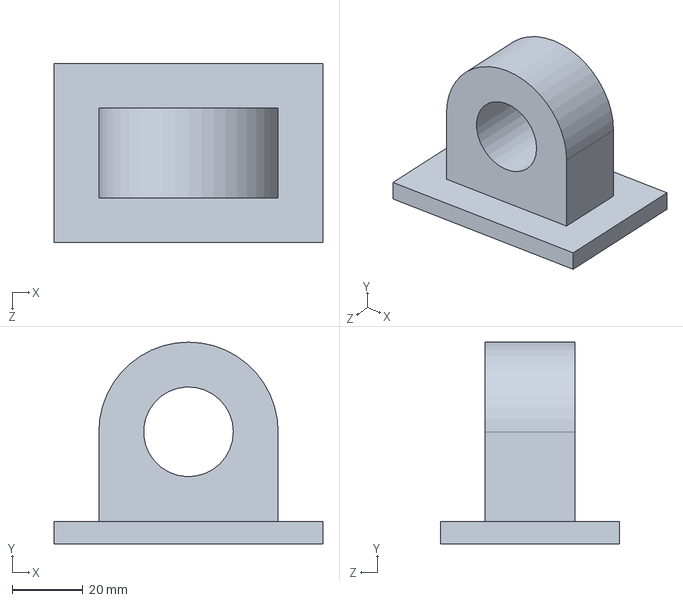
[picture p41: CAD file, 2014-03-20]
Design/Solidworks Models/Frame Optimization REV 2/piston pin bracket.SLDPRT
76.2 x 57.1 x 50.8 mm

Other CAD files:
Design/Solidworks Models/Frame Optimization REV 2/Piston mount plate.SLDPRT
Design/Solidworks Models/Frame REV 2_2/Foot side gussetts.SLDPRT
Design/Solidworks Models/Frame Optimization REV 2/Crossbeam 2.0.SLDPRT
Design/Solidworks Models/Frame Optimization REV 2/Piston crossbeam.SLDPRT
Design/Solidworks Models/Frame Optimization REV 2/2ft foot beam.SLDDRW
Design/Solidworks Models/Frame Optimization REV 2/2x2 foot gussetts.SLDPRT
Design/Solidworks Models/Frame Optimization REV 2/Crossbeam 2.0.SLDDRW
Design/Solidworks Models/Frame Optimization REV 2/Foot side gussetts.SLDPRT
Design/Solidworks Models/Frame Optimization REV 2/Frame Assembled with top side view.SLDDRW
Design/Solidworks Models/Frame Optimization REV 2/Frame Assembled with top.SLDDRW
Design/Solidworks Models/Frame Optimization REV 2/Main Frame.SLDDRW
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

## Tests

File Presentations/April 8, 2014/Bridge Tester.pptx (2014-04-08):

## Bridge Tester ELM-4702 Projects II

Ben Holleran
Carter Mealey

## What We Will Discuss

- The background of the project
- Our solution
- System diagrams
- Areas of responsibility
- Estimated Timeline
- Budget
- Conclusion

## Project Background

- Design and build testing equipment compatible with Trotski Competition
- Design project to be open source

Budget | $3500
Clients | John Diebold Gordon Reynolds

## Troitsky Competition

- Concordia University
- Colleges compete to build the strongest bridge
- Strongest bridge was made by MIT and held over six tons

Load display

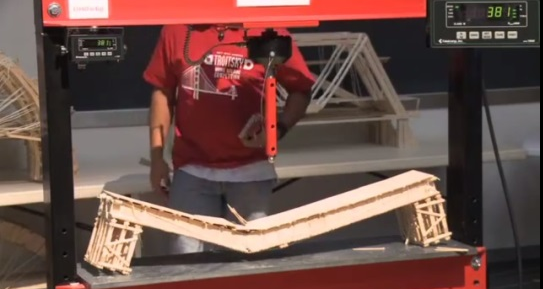
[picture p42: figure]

Crushed Bridge

Piston and piston extender

## Troitsky Competition

- Started in 1984
- 1991 first US team
- 1994, crusher exploded.
  - Mark on ceiling, Oil everywhere.
- New crusher, max 6000lb
- 2000 new crusher. Hydraulic jack
- 2010 new crusher. Hydraulic jack

## Design Specifications

- 1 meter span
- 10 Tons
- Mobile enough to move between buildings
- Load display visible across Judd Gym
- Accurate to 1% Load
- Precise to 1% between bridges
- 14” Piston Throw – Allows different height bridges to be tested

## Final Design

- Hydraulic Cylinder
- Truss instead of I-Beam to save weight
- Raspberry Pi as controller
  - HDMI monitor for force over deflection readout
  - I²C interface
    - 4” LED 7 segment display for load
    - Deflection data
    - Load data

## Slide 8

System Diagram

Large 7-Segment Display

LCD Screen

Bridge Goes Here

HDMI Cord

Hydraulic
Cylinder

Control box:
- Raspberry Pi
- I2C A2D
  - Force
  - Deflection
- Switches

Pressure
Line

Hydraulic Pump

3in x 3in Hollow
Steel

Large Castors

## Hydraulic Subsystem

1 ½ NPT

¾ NPT

¾-16

½ NPT

¼ NPT

Valve has built in pressure relief

Pressure Sensor

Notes: Our hydraulic system has is manually operated and has active extend and retract states. It is capable of outputting between 2K-3Ksi of pressure. It has a return tank and a gear pump with a manual handle.

## The Frame

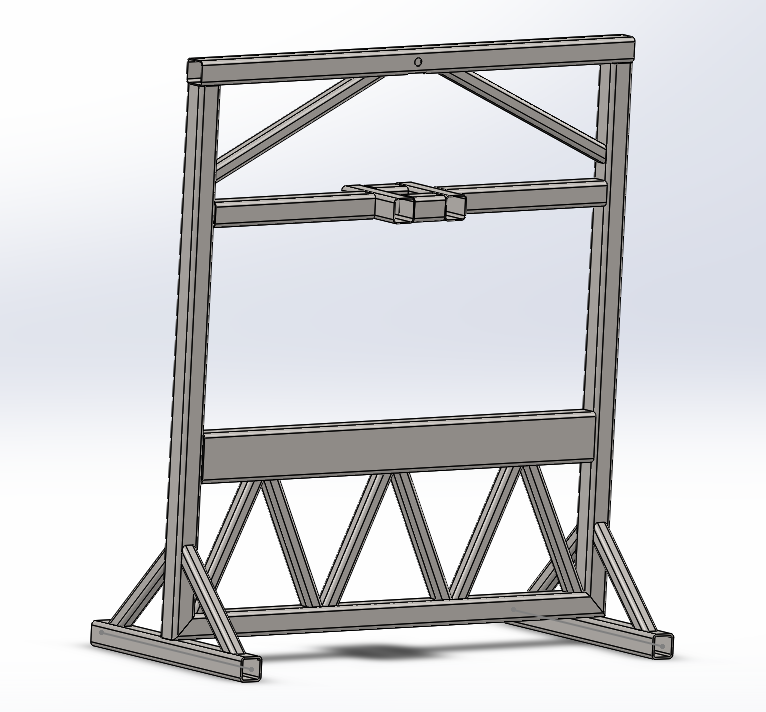
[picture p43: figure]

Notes: The frame is the structure that everything else is built on with this project. The above frame on the left shows the structure under maximum load with very exaggerated displacement visuals. There are a few more beams to be added to the frame but we are waiting on other key parts to fabricate mounting requirements after measurements.

## The Frame

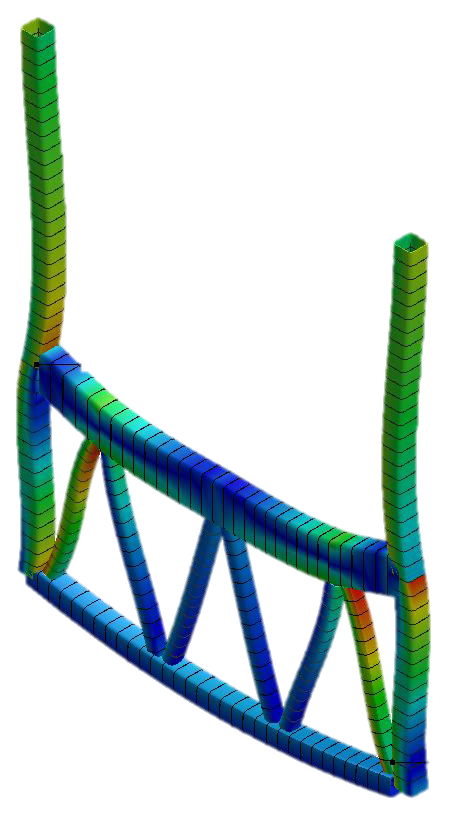
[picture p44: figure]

Minimum Safety Factor is 4

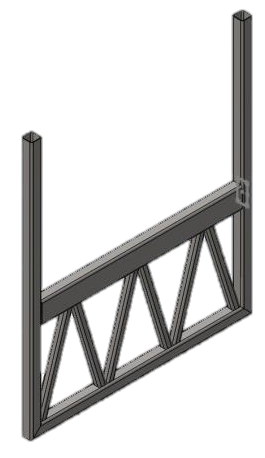
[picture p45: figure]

Truss Is lighter and stiffer than I beam

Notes: The frame is the structure that everything else is built on with this project. The above frame on the left shows the structure under maximum load with very exaggerated displacement visuals. There are a few more beams to be added to the frame but we are waiting on other key parts to fabricate mounting requirements after measurements.

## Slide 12

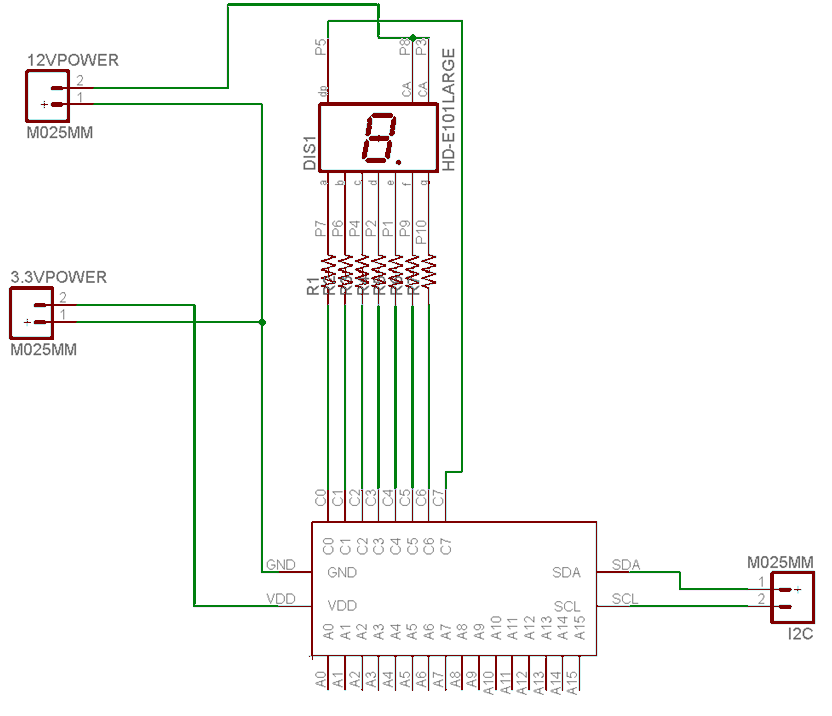
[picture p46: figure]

I²C 7 segment schematic

60 ohm

5 identical units will be built, and then given unique addresses

## Motor to Hydraulic Pump

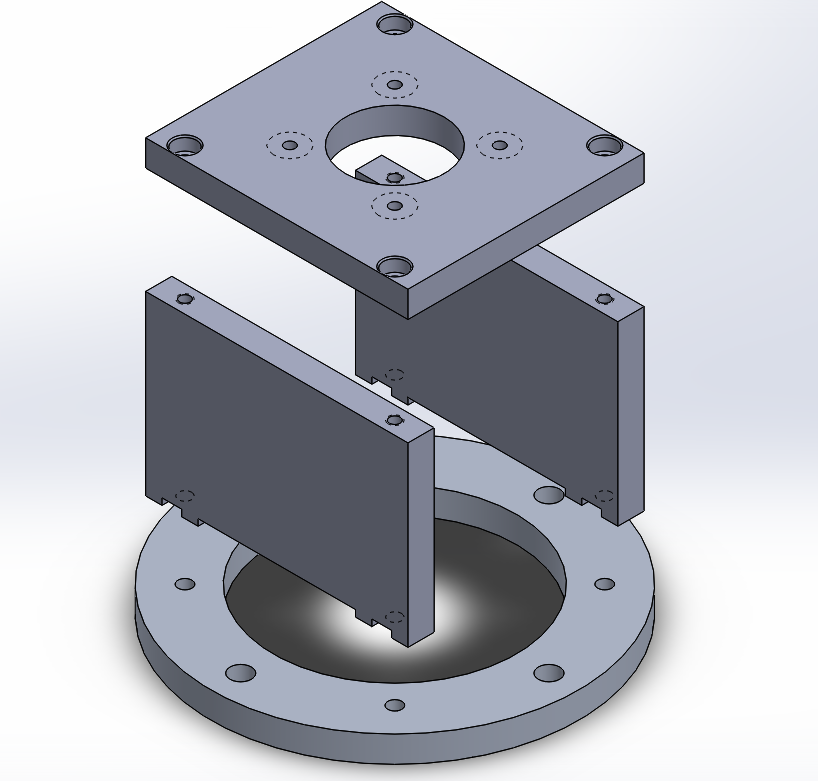
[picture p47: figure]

## Motor Adaptor Plate

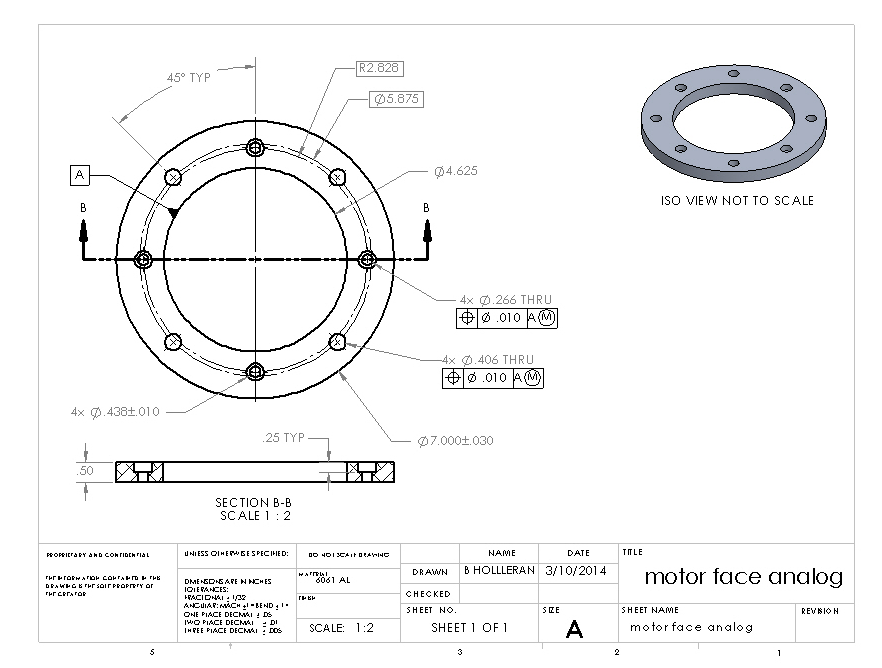
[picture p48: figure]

## Current Project Status

- Frame is welded.
- Piston mounting system is designed.
- Load display is designed.
- Software is designed.
- Hydraulics are waiting on bracket to be mounted.
- Frame needs more work to be ready to paint.
- Load display needs to be built
- Software needs to be written.

## Work Breakdown

Project managed on GitHub

- Put Gaant chart screen shot here

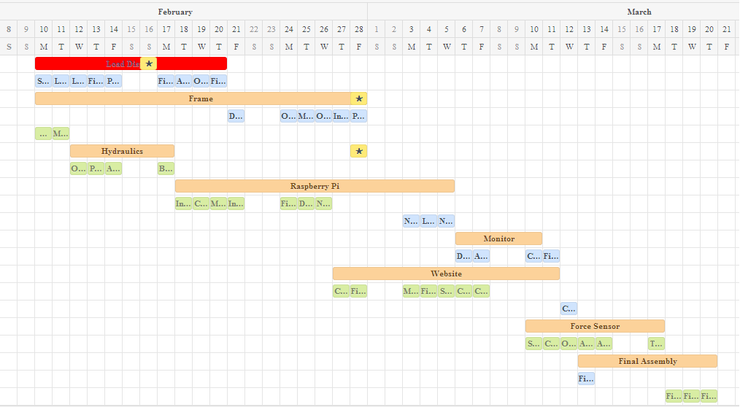
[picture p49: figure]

Carter
Ben

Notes: Here is our gaant chart with individual responsibilities and subsystems for each category. It shows due dates and what needs to be done in what order. It is available through our website via a link.

## Final Budget

Name | Qt | Price | Shipping | Total
Electronics | | | | | $ 600.95
7 segment display | 5 | $ 16.46 | $ 15.00 | $ 97.30
Rasberry Pi | 1 | $ 55.00 | $ 12.72 | $ 67.72
Monitor | 1 | $ 136.00 | $ - | $ 136.00
hdmi cord | 1 | $ 5.79 | $ - | $ 5.79
i2c ADC | 1 | $ 14.95 | $ 4.07 | $ 19.02
Switches | 1 | $ 5.95 | $ - | $ 5.95
Misc | 1 | $ 150.00 | $ - | $ 150.00
Darlington Array | 6 | $ 2.00 | $ 4.43 | $ 16.43
USB external HDD | 1 | $ 28.00 | $ 7.49 | $ 35.49
7-Seg I2C | 5 | $ 5.95 | $ 7.50 | $ 37.25
Wireless router | 1 | $ 30.00 | $ - | $ 30.00
| | | | $ -
Hydraulics | | | | | $ 1,676.16
Pump | 1 | $ 171.75 | $ 24.32 | $ 196.07
Motor | 1 | $ 123.00 | $ - | $ 123.00
Cylinder | 1 | $ 236.50 | $ - | $ 236.50
Sensor (0-5V) | 1 | $391.50 | $ - | $ 391.50
Lines | 5 | $ 100.00 | $ - | $ 500.00
Valve | 1 | $ 85.00 | $ - | $ 85.00
Tank | 1 | $ 70.00 | $ - | $ 70.00
Filter housing | 1 | $ 40.00 | $ - | $ 40.00
Filter Cartridge | 1 | $ 20.00 | $ - | $ 20.00
| | | $ - | $ -
Motor Coupling | 1 | $ 4.22 | $ - | $ 4.22
Pump Coupling | 1 | $ 5.29 | $ - | $ 5.29
Coupling Spider | 2 | $ 2.29 | $ - | $ 4.58
| | | $ - | $ -
| | | | $ -
Mechanical | | | | | $ 491.52
Castors | 4 | $ 47.88 | $ - | $ 191.52
Misc Hardware | 1 | $ 300.00 | $ - | $ 300.00
| | | $ - | $ -
| | | $ - | $ -
| | | $ - | $ -
| | | $ - | $ -
| | | $ - | $ -
| | | $ - | $ -
| | | $ - | $ -
Raw Materials | | | | | $ 315.21
Frame Steel | 0 | $ - | $ - | $ -
0 | .00 ft | $ 2.33 | $ - | $ -
0 | .00 ft | $ 3.63 | $ - | $ -
0 | .00 ft | $ 12.06 | $ - | $ -
Steel Cuts at Capitol | 6 | $ 10.00 | $ - | $ 60.00
| | $ - | $ - | $ -
| | $ - | $ - | $ -
Paint | 10 | $ 7.00 | $ - | $ 70.00
Aluminum plate 1'x6'x.5" | 1 | $ 185.21 | $ - | $ 185.21

Category | Total
Electronics | $ 600.95
Hydraulics | $ 1,676.16
Mechanical | $ 491.52
Raw Materials | $ 565.43
Total | $ 3,334.06

## Conclusion

- In Conclusion:
  - Design meets Client specs
  - Design is constructible within timeframe
  - Design is within budget

## Questions?

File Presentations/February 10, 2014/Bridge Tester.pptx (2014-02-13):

## Bridge Tester

Ben Holleran
Carter Mealey

## What We Will Discuss

- The background of the course and project
- Our solution
- System diagrams
- Areas of responsibility
- Estimated Timeline
- Budget
- Conclusion

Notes: We will discuss the background of our project and the course goals. We will also go over our solution to the selected project and show our system diagram. Areas of responsibility will be reviewed as well as a timeline and budget.

## Course Background

- Student design project
  - Vermont Technical College senior projects
    - Select project from list provided
    - Communicate with client to determine specs
    - Create design to meet specs
    - Review design with client and project managers
      - Create new specs and adjust design direction
    - Revise design to reflect changes
    - Build design while working with client
    - Final presentation

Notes: This course is a year long course spread over the two senior semesters. We were tasked with picking a project from a supplied list of clients and projects. For our projects we must communicate with our clients and create a design that fulfills the design requirements. As the project progresses and matures, meetings with the clients will continue to show progress and address concerns. The design will be revised to reflect the changes that the client requests. At the end of April the projects will be demonstrated and presented.

## Project Background

- Selected project: Bridge Tester
  - Design and build testing equipment compatible with Trotski Competition
  - Design project to be open source

Maximum Budget | $7000
Clients | John Diebold Gordon Reynolds

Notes: Our project is to build a bridge tester that is compatible with the Troitski Bridge Competition in April. Our clients are John Diebold and Gordon Reynolds who are both Architecture professors at VTC. We were given a maximum design budget of around $7000 to work with. We added an extra specification to our project that it should be open source so other schools can make their own based on our design.

## Final Specs

- 1 meter span – Troitski Competition compatible
- 10 Tons – Allows for shorter span bridges to be tested
- Mobile enough to move between buildings
- Load display visible across Judd Gym
- Accurate to 1% Load
- Precise to 1% between bridges
- 14” Piston Throw – Allows different height bridges to be tested

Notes: We are basing our design off the tester used at the Troitski competition in Montreal. We hope to make a tester that will allow the students here at VTC to practice by testing bridges here before going up to Montreal. We also hope that by making the tester available here at VTC, we can hold competitions for the local high schools and potentially colleges in the region.
We have worked out some of the preliminary specs with the architecture professors:
The tester will have the ability to test a bridge with a 1 meter span.
The current record at the Troitski competition is only 3.2 tons, so we will make our tester strong enough to break a bridge with 5 tons.
One of the things that we noticed while looking at the current Troitski tester is that it is very heavy and hard to move around. We will be designing our tester so it can be moved into Judd gym by two people. This means it needs to be able to be carried down stairs and fit through a single standard door.
We will be trying to make the tester accurate to within 1%. This means that the displayed load will be within 1% of the true force applied to the bridge
We will also try to ensure that the Displayed load will be precise to within 1 lb, the smallest unit we will be measuring, between competitions. This will ensure that a bridge breaking at 501lb really did take more force than the bridge that broke at 500lb earlier that afternoon.
The tester will have a 14” throw enabling the competition to “serve” bridges of different heights

## Final Design

- Hydraulic Cylinder
- Truss instead of I-Beam to save weight
- Raspberry Pi as controller
  - HDMI monitor for force over deflection readout
  - I²C interface
    - 4” LED 7 segment display for load
    - Deflection data
    - Load data
  - Web interface to download logs.

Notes: Our preliminary design consists of a hydraulic cylinder fixed to the top of a truss frame design. The frame must fit a bridge with a span of a meter within it. The hydraulic cylinder has a stroke of 14” which should allow for plenty of reach. We are using a steel truss design over an I-Beam design in order to save overall weight while maintaining high structural strength and rigidity. A 7-Segment with 4” tall characters will be used to allow the audience to clearly see the current load value from a distance. A Raspberry Pi microcomputer will be used as the main controller for our project. It has the power of a standard computer with the low price and super small size of a microcontroller. An LCD screen with a custom GUI showing deformation in live time will be connected directly to the Raspberry Pi using an HDMI cable. A web interface will also be designed to allow for the downloading of run logs from remote locations.

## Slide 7

Large 7-Segment Display

8888

Bridge Goes Here

LCD Screen

HDMI Cord

Hydraulic
Cylinder

Pressure
Line

Control box:
- Raspberry Pi
- I2C A2D
  - Force
  - Deflection
- Switches

3in x 3in Hollow
Steel Tubing Frame

Hydraulic Pump

Large Castors

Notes: Our design consists of a steel frame with trusses made from 2in square tubing. This allows for great strength while maintaining relatively low weight. There is a hydraulic cylinder with a large throw of around 14”. The cylinder is pressurized with a large hydraulic pump powered by an electric motor. There is a control box on the side of the frame for the operator to control the tester. There is a Raspberry Pi inside control box that controls 7-Segment display, the LCD screen, hydraulic pump, and reads the pressure gauge using various interface methods all translated over the GPIO pins. The frame is on wheels for easy mobility.

## Work Breakdown

Areas of Responsibility | | | | Mechanical
Ben | | Carter | | Electrical
Hydraulics | | Frame | | Software
Force Sensor | | Monitor and 7-Segment
HDMI Display GUI | | HDMI Display GUI
Mounting Points on Frame | | Mounting Points on Frame
Website | | Website

## Final Budget

Name | Qt | Price | Shipping | Total
Electronics | | | | | $ 600.95
7 segment display | 5 | $ 16.46 | $ 15.00 | $ 97.30
Rasberry Pi | 1 | $ 55.00 | $ 12.72 | $ 67.72
Monitor | 1 | $ 136.00 | $ - | $ 136.00
hdmi cord | 1 | $ 5.79 | $ - | $ 5.79
i2c ADC | 1 | $ 14.95 | $ 4.07 | $ 19.02
Switches | 1 | $ 5.95 | $ - | $ 5.95
Misc | 1 | $ 150.00 | $ - | $ 150.00
Darlington Array | 6 | $ 2.00 | $ 4.43 | $ 16.43
USB external HDD | 1 | $ 28.00 | $ 7.49 | $ 35.49
7-Seg I2C | 5 | $ 5.95 | $ 7.50 | $ 37.25
Wireless router | 1 | $ 30.00 | $ - | $ 30.00
| | | | $ -
Hydraulics | | | | | $ 1,676.16
Pump | 1 | $ 171.75 | $ 24.32 | $ 196.07
Motor | 1 | $ 123.00 | $ - | $ 123.00
Cylinder | 1 | $ 236.50 | $ - | $ 236.50
Sensor (0-5V) | 1 | $391.50 | $ - | $ 391.50
Lines | 5 | $ 100.00 | $ - | $ 500.00
Valve | 1 | $ 85.00 | $ - | $ 85.00
Tank | 1 | $ 70.00 | $ - | $ 70.00
Filter housing | 1 | $ 40.00 | $ - | $ 40.00
Filter Cartridge | 1 | $ 20.00 | $ - | $ 20.00
| | | $ - | $ -
Motor Coupling | 1 | $ 4.22 | $ - | $ 4.22
Pump Coupling | 1 | $ 5.29 | $ - | $ 5.29
Coupling Spider | 2 | $ 2.29 | $ - | $ 4.58
| | | $ - | $ -
| | | | $ -
Mechanical | | | | | $ 491.52
Castors | 4 | $ 47.88 | $ - | $ 191.52
Misc Hardware | 1 | $ 300.00 | $ - | $ 300.00
| | | $ - | $ -
| | | $ - | $ -
| | | $ - | $ -
| | | $ - | $ -
| | | $ - | $ -
| | | $ - | $ -
| | | $ - | $ -
Raw Materials | | | | | $ 315.21
Frame Steel | 0 | $ - | $ - | $ -
0 | .00 ft | $ 2.33 | $ - | $ -
0 | .00 ft | $ 3.63 | $ - | $ -
0 | .00 ft | $ 12.06 | $ - | $ -
Steel Cuts at Capitol | 6 | $ 10.00 | $ - | $ 60.00
| | $ - | $ - | $ -
| | $ - | $ - | $ -
Paint | 10 | $ 7.00 | $ - | $ 70.00
Aluminum plate 1'x6'x.5" | 1 | $ 185.21 | $ - | $ 185.21

Category | Total
Electronics | $ 600.95
Hydraulics | $ 1,676.16
Mechanical | $ 491.52
Raw Materials | $ 565.43
Total | $ 3,334.06

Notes: We were given a budget of around $7000. At this point in time we have done some the vast majority of the pricing and parts selected. Our current budget is just shy of $3400 with hydraulics taking up half of that amount and the remaining categories are all around 15-18% each.

## Project Management

Project managed on GitHub

- Put Gaant chart screen shot here


Carter
Ben

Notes: Here is our gaant chart with individual responsibilities and subsystems for each category. It shows due dates and what needs to be done in what order. It is available through our website via a link.

## Website

- Found server to host on
- Found template
- Need to add content
- Need to migrate to VTC servers

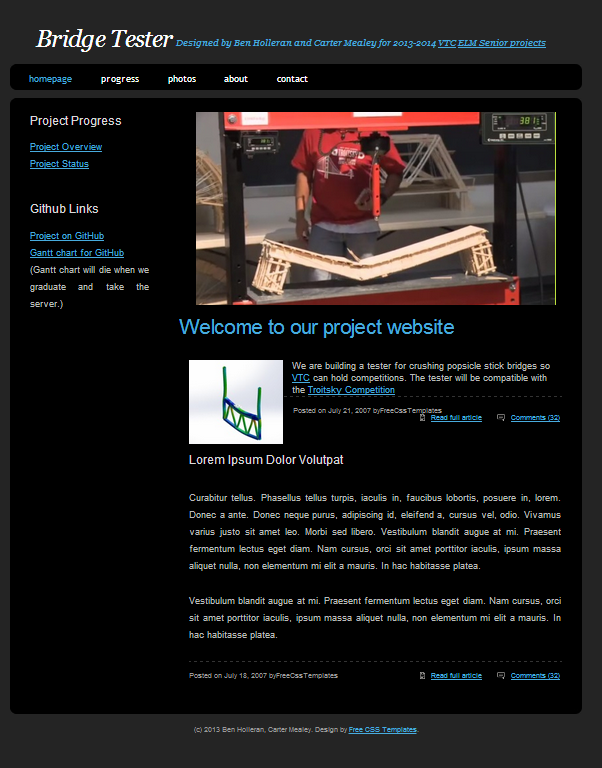
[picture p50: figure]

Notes: We currently have a website hosted on a private server here on campus. It showcases our project and has links to various subsections of our project like our gaant chart. It is currently unfinished and is a work in progress. As the semester continuous the website will be moved to the VTC servers to be preserved after graduation.

## Hydraulic Subsystem

1 ½ NPT

¾ NPT

¾-16

½ NPT

¼ NPT

Valve has built in pressure relief

Pressure Sensor

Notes: Our hydraulic system has is manually operated and has active extend and retract states. It is capable of outputting between 2K-3Ksi of pressure. It has a return tank and a gear pump with a manual handle.

## The Frame


Minimum Safety Factor is 2


Truss Is lighter and stiffer than I beam

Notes: The frame is the structure that everything else is built on with this project. The above frame on the left shows the structure under maximum load with very exaggerated displacement visuals. There are a few more beams to be added to the frame but we are waiting on other key parts to fabricate mounting requirements after measurements.

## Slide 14

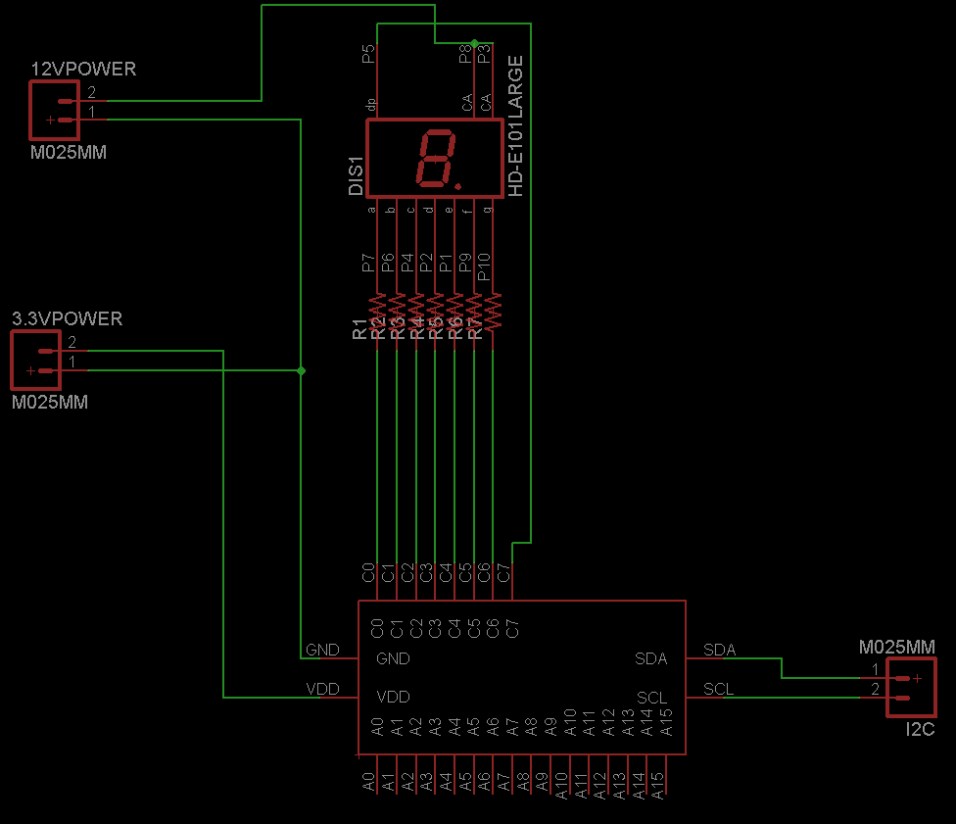
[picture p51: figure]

I²C 7 segment schematic

60 ohm

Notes: This is the I2C 7-Segment display in it’s pure electrical schematic. The I2C chip used has the power required to operate 7-Segment display with the 12V power. The display it’s self is a 4in digit with 5 of these digits to vividly display the maximum load value.

## Current Project Status

- Parts are identified and budget is finalized.
- Ordering is to begin the week of 2/9/14
- Testing and assembly of select subsystems is currently in progress (A2D converter)

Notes: The budget is finished and there are a lot of parts to be ordered starting this week. Testing has begun on some smaller subsystems such as the A2D converter.

## Conclusion

- In Conclusion:
  - Design meets Course specs
  - Design meets Client specs
  - Design is constructible within timeframe
  - Design is within budget

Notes: Our project fulfills all of the requirements for the class. It has the required amount of mechanical, electrical, and software specifications. Our design fulfills the specifications of Mr. Diebolds the client. Our project will be able to be constructed in a timely fashion and will fall within our budget constraints.

## Questions?

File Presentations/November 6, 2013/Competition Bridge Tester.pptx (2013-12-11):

## Competition Bridge Tester

Carter Mealey
Ben Holleran

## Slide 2

## Preliminary Specs

- 1 meter Span – Trotski Competition
- 5 Tons – Current Record 3.2 Tons
- Movable by Two People
- Displays Load on Large Display
- Accurate to 1% Load
- Precise to 1 lb During competition
- 8” Piston Throw

## Preliminary Calculations

- 1020 Cold Rolled Mild Steel – Easily Welded
  - 43.5 KSI Yield
  - (Yield Strength)/(Area) = Max Elastic Force
  - 2” Square Tubing 1/16” Wall = .484 in² = 10.5 Tons
  - 2” Square Tubing 1/8” Wall = .9375 in² = 20.4 Tons
- 5 Tons
  - Area=(Force)/(Pressure) = (5 Tons=10,000lb)/(1000 PSI) = 10 in²
  - A = πr² √(A/π) = r = √((10 in2)/3.14159) = 1.78 in = 3.6⌀” Piston

## Brainstorming

## Tech to use / Research

## Communication

## Research results

## System Diagram

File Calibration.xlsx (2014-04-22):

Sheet: Data2
Gain |  | 1875 | 26.21475407
Reading | Ring | Calculated LBS | Piston Offset | Correction
218 | 40 | 431.0765288 | 25.86965914 | 1.858747108
249 | 47 | 501.6105547 | 38.78252473 | 2.01450022
388.22 | 74 | 773.6703691 | 52.06756667 | 1.992865821
532.22 | 100 | 1035.653894 | 46.39150801 | 1.945913145
554.91 | 104 | 1075.959052 | 44.5216938 | 1.938979387
672.9 | 123 | 1267.408551 | 16.65762148 | 1.883502082
742.12 | 135 | 1388.324024 | 8.910619693 | 1.870754088
775.12 | 142 | 1458.85805 | 18.10599106 | 1.882106061
879.94 | 156.5 | 1604.964246 | -30.62168423 | 1.823947367
2714.25 | 502 | 5086.322241 | 41.21790234 | 1.873932851
3524.5 | 650 | 6577.613076 | 26.45889208 | 1.866254242
Gain | 4 |  | 69.1778227
Reading | Ring | Calculated | Piston Offset | Correction
2639.42 | 391.5 | 3972.89226 | -670.8228345 | 1.759369519
2639.42 | 391.5 | 3972.89226 | -670.8228345 | 1.505214123
1272 | 238 | 2426.181834 | 188.2638065 | 1.907375656
1569.25 | 290 | 2950.148884 | 189.258267 | 1.879973799
1768 | 333 | 3383.429329 | 272.8640202 | 1.913704372
1912.62 | 352 | 3574.878828 | 209.8734995 | 1.869100411
2462.25 | 451 | 4572.431481 | 240.4238836 | 1.857013496
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

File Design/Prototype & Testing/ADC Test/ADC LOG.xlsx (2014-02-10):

0:00:00 | 0.0002413739217 | 1576.25 | #REF! | 12610 | 12606.95701
0:00:00 | 0.0002413739217 | 1576.25 | #REF! | 12610
0:00:00 | 8.273135646e-05 | 1576 | #REF! | 12608
0:00:00 | 8.273135646e-05 | 1576 | #REF! | 12608
0:00:00 | 8.273135646e-05 | 1576 | 6.686709993e-05 | 12608
0:00:01 | 8.273135646e-05 | 1576 | 6.109827938e-05 | 12608
0:00:01 | 3.410073832e-06 | 1575.88 | 3.94652023e-05 | 12607
0:00:01 | 3.410073832e-06 | 1575.88 | 3.410073832e-06 | 12607
0:00:01 | -0.0001552324914 | 1575.63 | -1.101197755e-05 | 12605
0:00:01 | 3.410073832e-06 | 1575.88 | -3.985608033e-05 | 12607
0:00:01 | 3.410073832e-06 | 1575.88 | -6.87001831e-05 | 12607
0:00:01 | 3.410073832e-06 | 1575.88 | -9.033326018e-05 | 12607
0:00:01 | -0.0001552324914 | 1575.63 | -0.000119177363 | 12605
0:00:01 | -7.591120879e-05 | 1575.75 | -0.0001335994143 | 12606
0:00:01 | -0.000234553774 | 1575.5 | -0.0001480214657 | 12604
0:00:01 | -0.000234553774 | 1575.5 | -0.0001696545428 | 12604
0:00:02 | -0.0001552324914 | 1575.63 | -0.0001912876199 | 12605
0:00:02 | -0.0003138750567 | 1575.38 | -0.000234553774 | 12603
0:00:02 | -0.0001552324914 | 1575.63 | -0.0002489758254 | 12605
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

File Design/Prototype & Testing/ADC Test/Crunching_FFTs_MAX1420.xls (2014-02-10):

ENTER Data Record from ADC | ENTER fSAMPLE (Hz) | ENTER NRECORD | ENTER ADC Resolution (bits) | CALCULATED fBIN (MHz) | CALCULATED fNYQUIST (MHz) | CALCULATED FFT Bin Frequency (MHz) | Calculated # of data point | CALCULATED Time of data point (µs) | CALCULATED Maximum Data Record Point | CALCULATED Minimum Data Record Point | CALCULATED Magnitude of Data Record (dBFS) | FFT CALCULATION Imaginary FFT Points | CALCULATED FFT Magnitude | CALCULATED FFT/Nrecord | CALCULATED Log FFT Data | CALCULATED Final FFT Data | CALCULATED Maximum FFT Data Point | CALCULATED Shft between Log FFT and Final FFTshift
12610 | 10 | 1023 | 15 | 0.009775171065 | 5 | 0 | 0 | 0.00000 | 12615 | 12597 | -65.2035486 | 8537927 | 8537927 | 16691.93939 | 84.5 | 18.2 | 11.56343727 | 66.22524959
12610 |  |  |  |  |  | 0.009775171065 | 1 | 0.10000 |  |  |  | -3.28172314568638+5.41978267820257i | 6.335909649 | 0.01238692014 | -38.1 | -104.4
12608 |  |  |  |  |  | 0.01955034213 | 2 | 0.20000 |  |  |  | -37.0372275200552-37.8769799389544i | 52.97567207 | 0.1035692514 | -19.7 | -85.9
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

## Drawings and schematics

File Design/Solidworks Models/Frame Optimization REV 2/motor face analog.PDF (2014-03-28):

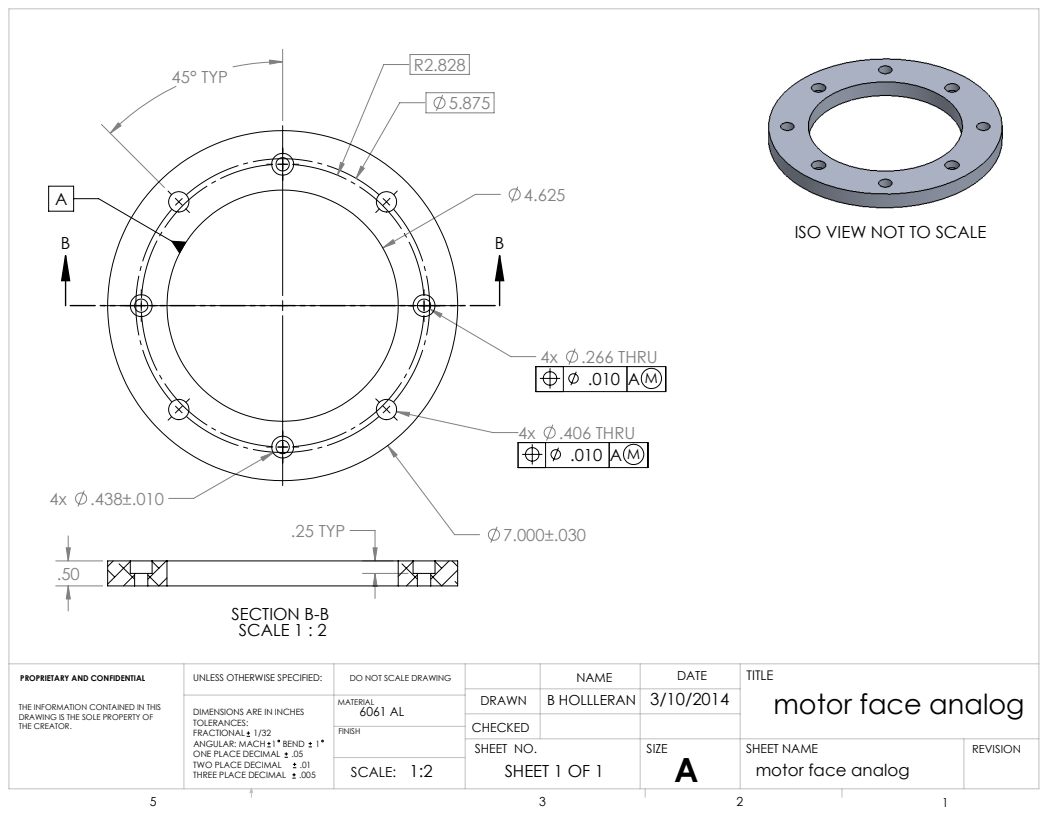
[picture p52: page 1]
45° TYP; 4x .266 THRU; 4x .406 THRU; .25 TYP; SECTION B-B SCALE 1 : 2; UNLESS OTHERWISE SPECIFIED:; DATE; SHEET NO.; motor face analog; TWO PLACE DECIMAL; B HOLLLERAN; SIZE; SHEET NAME; SHEET 1 OF 1

ISO VIEW NOT TO SCALE

PROPRIETARY AND CONFIDENTIAL

DO NOT SCALE DRAWING

THE INFORMATION CONTAINED IN THIS
DRAWING IS THE SOLE PROPERTY OF
THE CREATOR.

DIMENSIONS ARE IN INCHES
TOLERANCES:
FRACTIONAL 1/32
ANGULAR: MACH 1 BEND 1
ONE PLACE DECIMAL .05
THREE PLACE DECIMAL .005

motor face analog

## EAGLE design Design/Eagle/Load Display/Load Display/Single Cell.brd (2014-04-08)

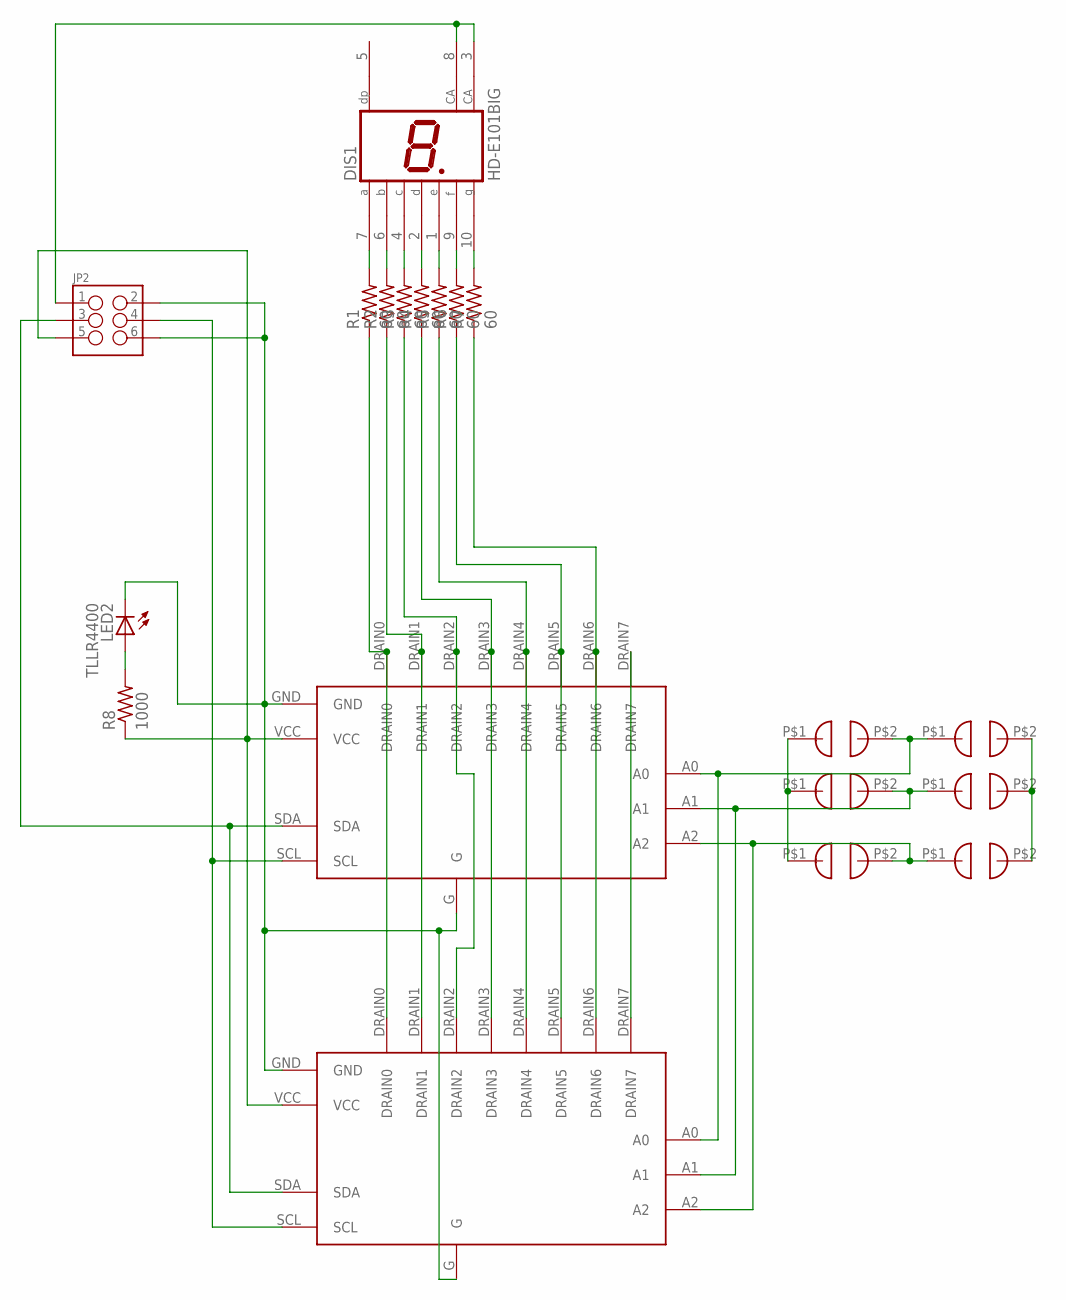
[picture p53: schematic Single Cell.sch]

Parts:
DIS1: HD-E101BIG; 7SEGMENT_BACKWARDS
JP2: M03X2SHROUD; 2X3-SHROUDED
LED2: TLLR4400; LED3MM
R1, R2, R3, R4, R5, R6, R7: 60; 0207/15
R8: 1000; 0207/15
U$1, U$3, U$4, U$5, U$6, U$7: SOLDER_JUMPER
U$2: LED_DRIVERBOARDADAFRUIT; DRIVER_BOARD_ADAFRUIT
U$8: LED_DRIVERBOARD; DRIVER_BOARD

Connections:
GND: JP2.2, JP2.6, LED2.K (C), U$1.P$1, U$2.G, U$2.GND, U$4.P$1, U$6.P$1, U$8.G, U$8.GND
unnamed: DIS1.7 (A), R1.2
unnamed: DIS1.6 (B), R2.2
unnamed: DIS1.4 (C), R3.2
unnamed: DIS1.2 (D), R4.2
unnamed: DIS1.1 (E), R5.2
unnamed: DIS1.9 (F), R6.2
unnamed: DIS1.10 (G), R7.2
unnamed: R1.1, U$2.DRAIN0, U$8.DRAIN0
unnamed: R2.1, U$2.DRAIN1, U$8.DRAIN1
unnamed: R3.1, U$2.DRAIN2, U$8.DRAIN2
unnamed: R4.1, U$2.DRAIN3, U$8.DRAIN3
unnamed: R5.1, U$2.DRAIN4, U$8.DRAIN4
unnamed: R6.1, U$2.DRAIN5, U$8.DRAIN5
unnamed: R7.1, U$2.DRAIN6, U$8.DRAIN6
unnamed: U$2.A1, U$4.P$2, U$5.P$1, U$8.A1
unnamed: U$2.A2, U$6.P$2, U$7.P$1, U$8.A2
unnamed: U$2.DRAIN7, U$8.DRAIN7
unnamed: LED2.A, R8.2
unnamed: U$1.P$2, U$2.A0, U$3.P$1, U$8.A0
SDA: JP2.3, U$2.SDA, U$8.SDA
SSCL: JP2.4, U$2.SCL, U$8.SCL
VCC5: JP2.5, R8.1, U$2.VCC, U$3.P$2, U$5.P$2, U$7.P$2, U$8.VCC
VCC12: DIS1.3 (CA), DIS1.8 (CA), JP2.1

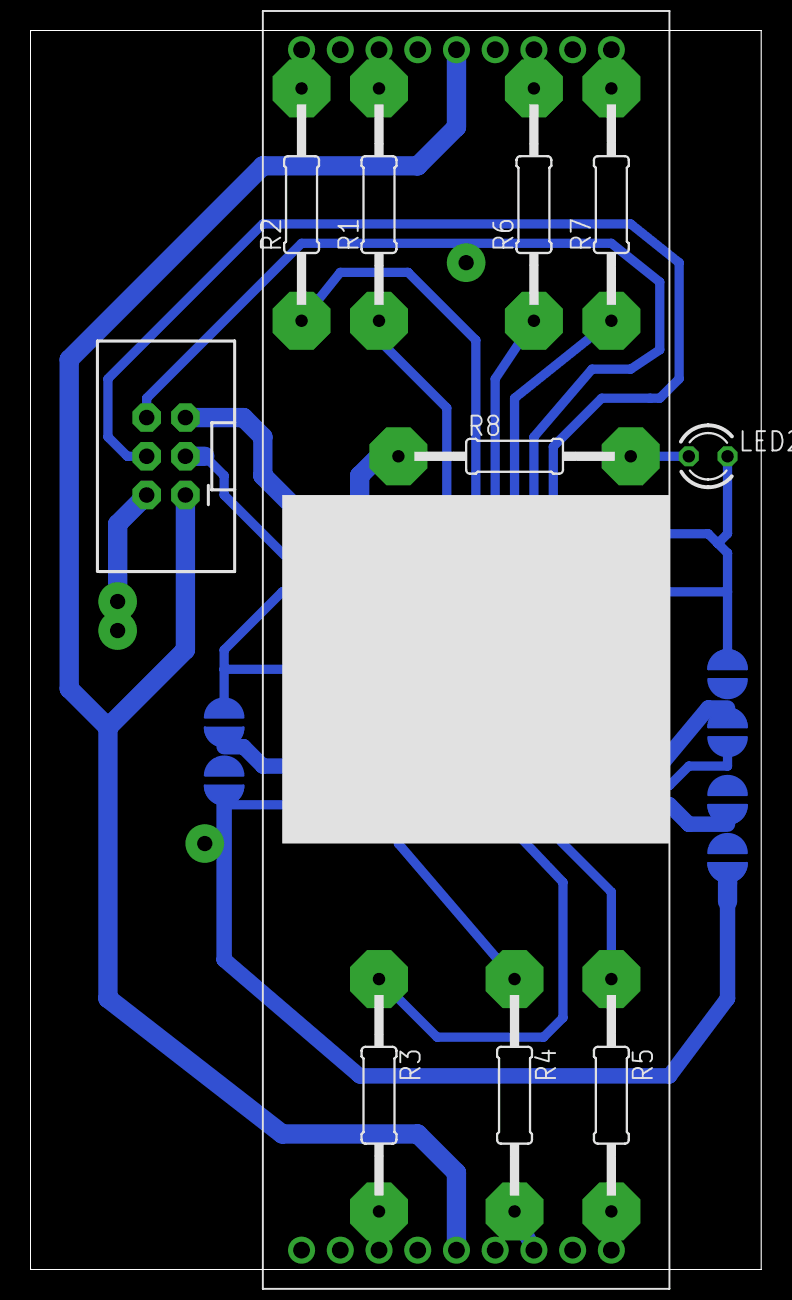
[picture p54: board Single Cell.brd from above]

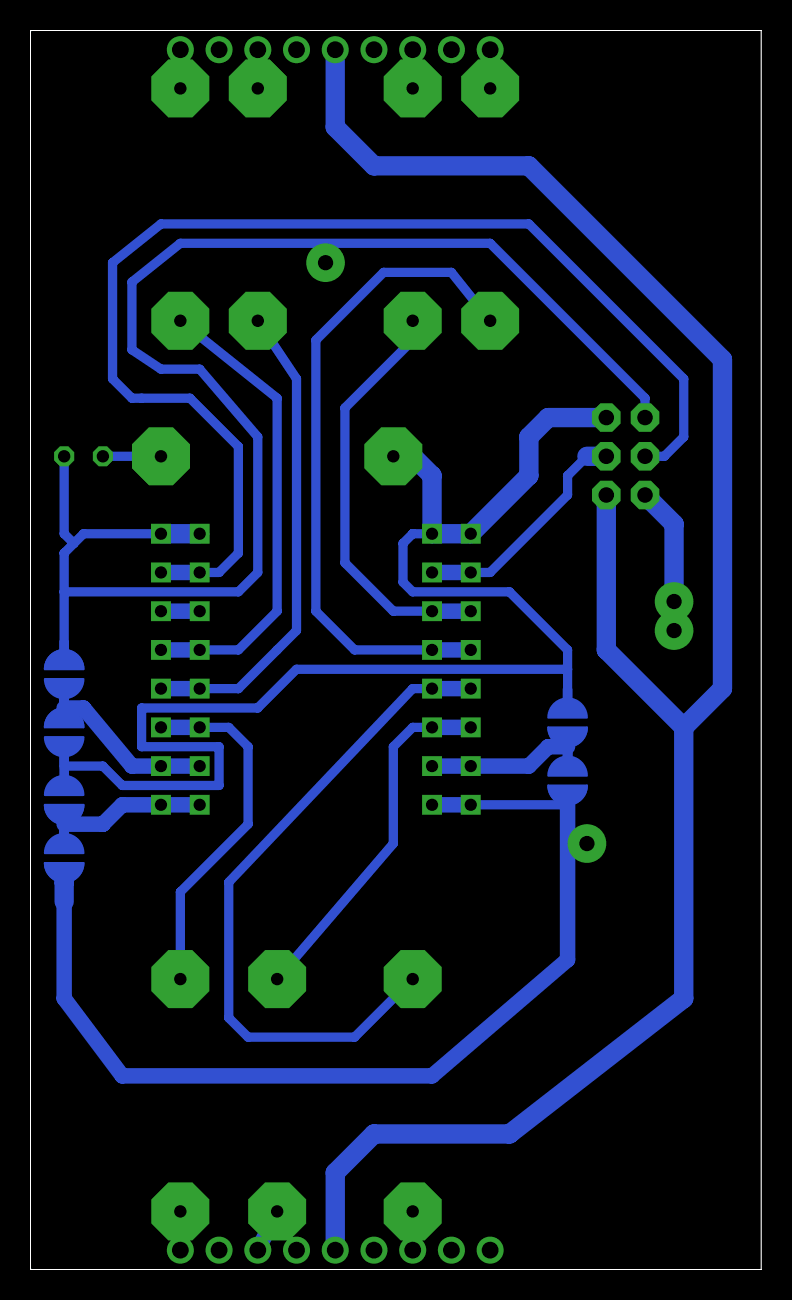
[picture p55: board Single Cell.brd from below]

Board: 2 copper layers, 47.9 x 81.3 mm, 19 parts (6 on the bottom side), 24 nets.

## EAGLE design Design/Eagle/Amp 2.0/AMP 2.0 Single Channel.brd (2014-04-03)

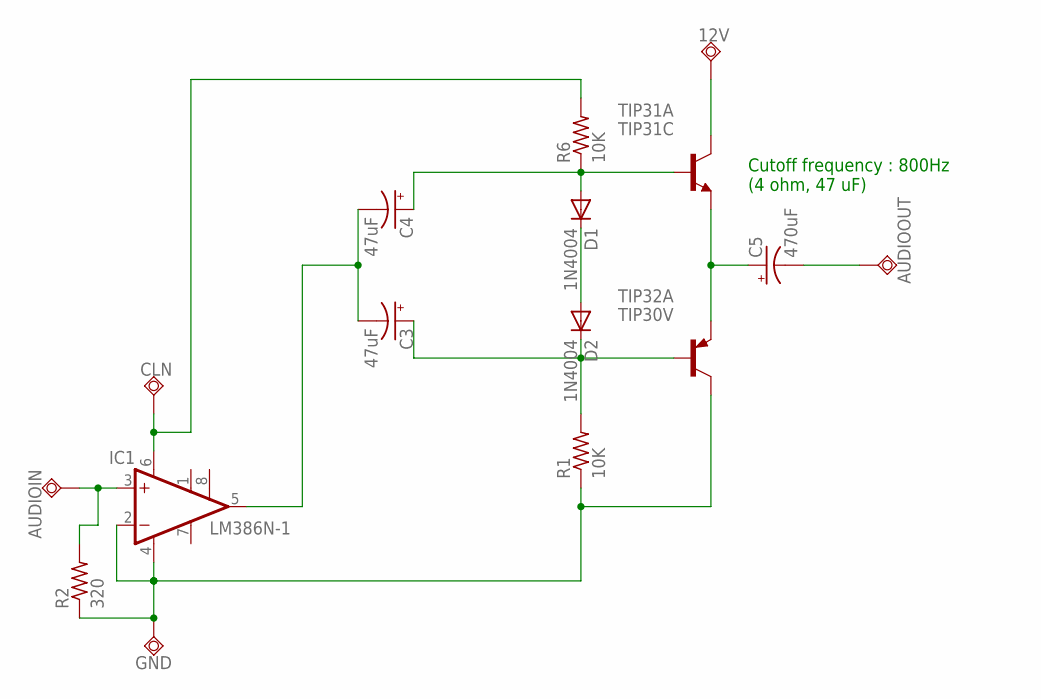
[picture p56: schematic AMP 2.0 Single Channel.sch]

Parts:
12V: TPSQPAD1-20; P1-20
AUDIOIN: TPSQPAD1-20; P1-20
AUDIOOUT: TPSQPAD1-20; P1-20
C3, C4: 47uF; E5-4
C5: 470uF; E5-4
CLN: TPSQPAD1-20; P1-20
D1, D2: 1N4004; DO41-10
GND: TPSQPAD1-20; P1-20
IC1: LM386N-1; DIL08
R1, R6: 10K; 0204/7
R2: 320; 0204/7
TIP31A: TIP31C; TO220V
TIP32A: TIP30V; TO220V

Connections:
AALFT: C3.-, C4.-, IC1.5 (OUT)
ALFT: AUDIOIN.TP, IC1.3 (+IN), R2.2
AULEFT: AUDIOOUT.TP, C5.-
CLEANPWR: C4.+, D1.A, R6.1, TIP31A.1 (B)
GND: GND.TP, IC1.2 (-IN), IC1.4 (GND), R1.1, R2.1, TIP32A.2 (C)
unnamed: D1.C, D2.A
unnamed: C3.+, D2.C, R1.2, TIP32A.1 (B)
unnamed: CLN.TP, IC1.6 (VS), R6.2
unnamed: C5.+, TIP31A.3 (E), TIP32A.3 (E)
unnamed: 12V.TP, TIP31A.2 (C)

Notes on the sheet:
Cutoff frequency : 800Hz (4 ohm, 47 uF)

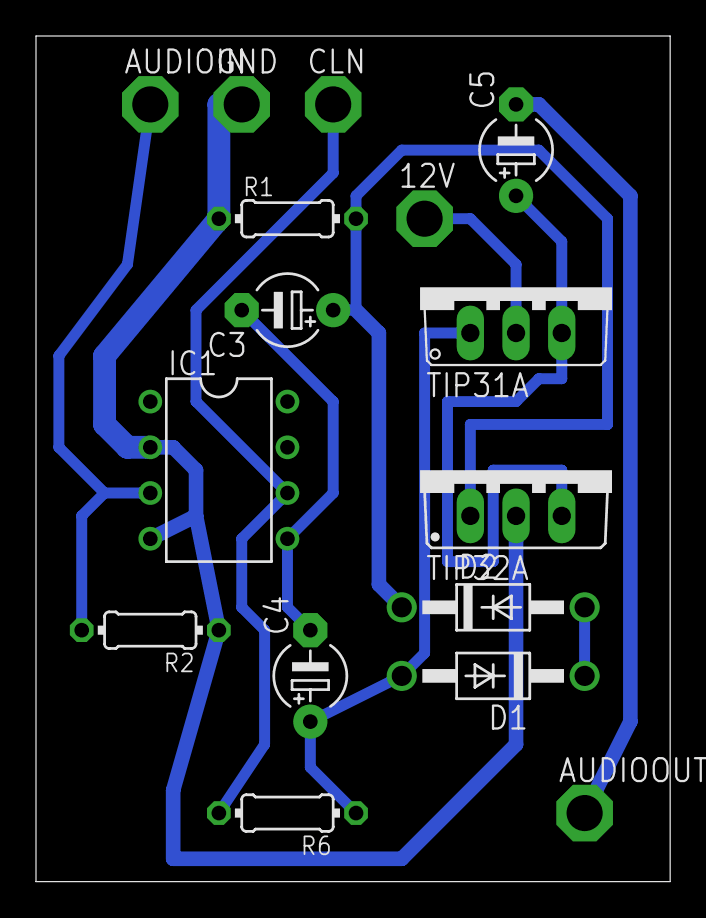
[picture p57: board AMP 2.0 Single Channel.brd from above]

Board: 2 copper layers, 35.2 x 47.0 mm, 16 parts (0 on the bottom side), 10 nets.

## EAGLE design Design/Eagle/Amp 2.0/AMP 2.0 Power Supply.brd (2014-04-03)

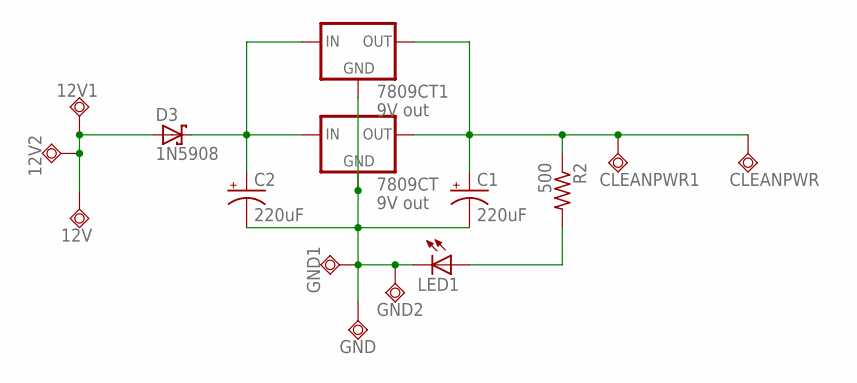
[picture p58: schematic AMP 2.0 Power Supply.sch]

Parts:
12V, 12V1, 12V2: TPSQPAD1-20; P1-20
7809CT, 7809CT1: 9V out; 78XXS
C1, C2: 220uF; B45181C
CLEANPWR, CLEANPWR1: TPSQPAD1-20; P1-20
D3: 1N5908; C4111-15
GND, GND1, GND2: TPSQPAD1-20; P1-20
LED1: LED5MM
R2: 500; 0204/7

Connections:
BUFFEREDDIRTY: 7809CT.IN, 7809CT1.IN, C2.+, D3.C
CLEAN9V: 7809CT.OUT, 7809CT1.OUT, C1.+, CLEANPWR.TP, CLEANPWR1.TP, R2.1
unnamed: 7809CT.GND, 7809CT1.GND, C1.-, C2.-, GND.TP, GND1.TP, GND2.TP, LED1.K (C)
unnamed: 12V.TP, 12V1.TP, 12V2.TP, D3.A
unnamed: LED1.A, R2.2

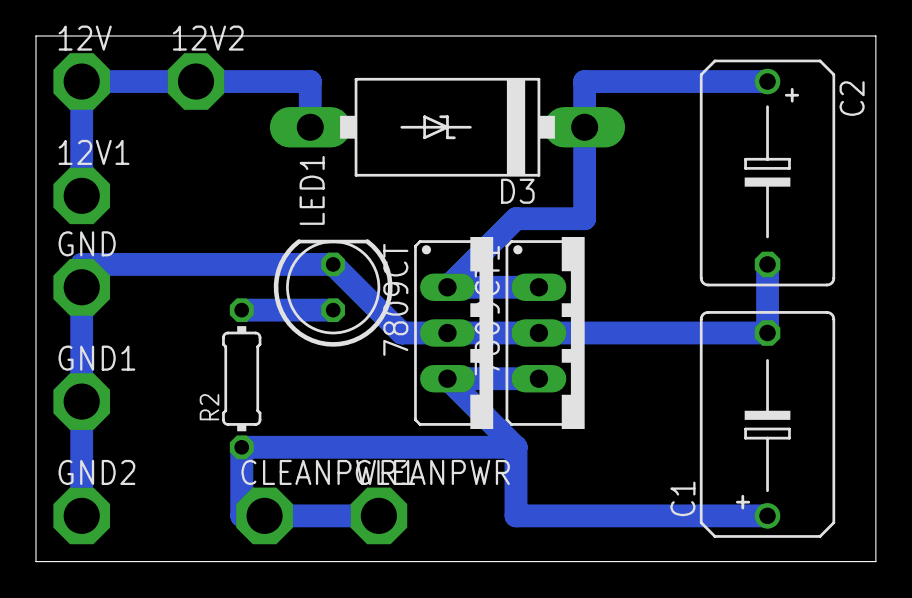
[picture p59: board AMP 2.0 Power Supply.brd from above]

Board: 2 copper layers, 46.7 x 29.2 mm, 15 parts (0 on the bottom side), 5 nets.

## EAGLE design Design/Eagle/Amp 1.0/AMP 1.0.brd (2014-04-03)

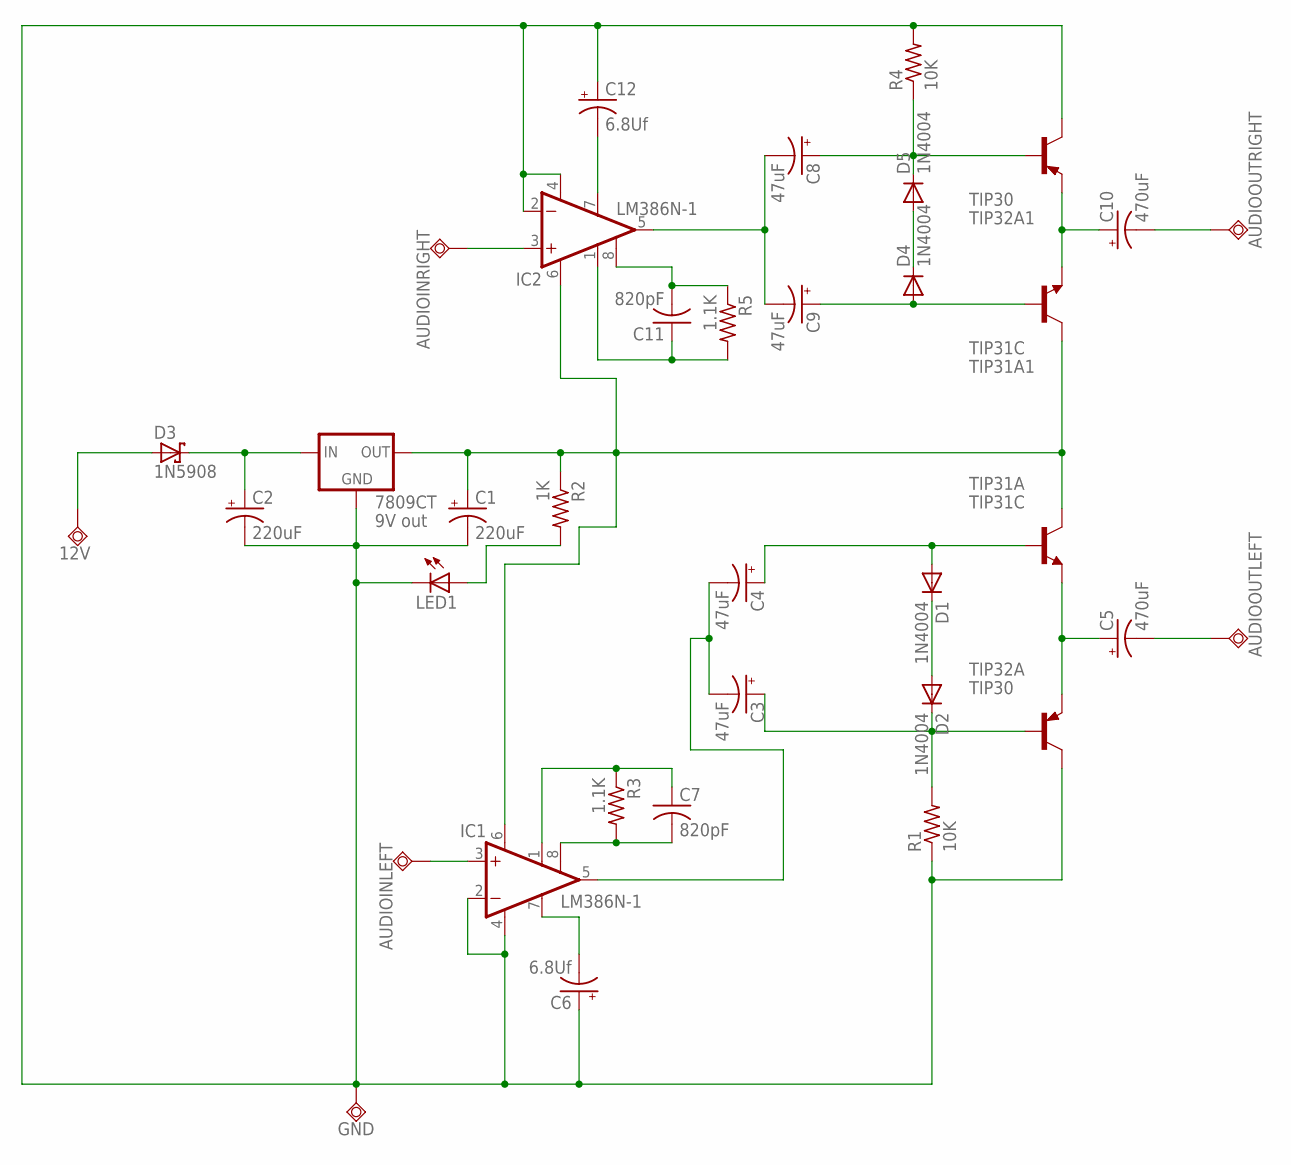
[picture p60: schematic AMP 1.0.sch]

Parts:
12V: TPSQPAD1-20; P1-20
7809CT: 9V out; 78XXL
AUDIOINLEFT: TPSQPAD1-20; P1-20
AUDIOINRIGHT: TPSQPAD1-20; P1-20
AUDIOOUTLEFT: TPSQPAD1-20; P1-20
AUDIOOUTRIGHT: TPSQPAD1-20; P1-20
C1, C2: 220uF; B45181C
C3, C4, C8, C9: 47uF; E5-4
C5, C10: 470uF; E5-4
C6, C12: 6.8Uf; E5-4
C7, C11: 820pF; C050-050X075
D1, D2, D4, D5: 1N4004; DO41-10
D3: 1N5908; C4111-15
GND: TPSQPAD1-20; P1-20
IC1, IC2: LM386N-1; DIL08
LED1: LED5MM
R1, R4: 10K; 0204/7
R2: 1K; 0204/7
R3, R5: 1.1K; 0204/7
TIP31A, TIP31A1: TIP31C; TO220
TIP32A, TIP32A1: TIP30; TO220

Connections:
unnamed: D1.C, D2.A
unnamed: C3.+, D2.C, R1.2, TIP32A.1 (B)
unnamed: C4.+, D1.A, TIP31A.1 (B)
unnamed: C5.+, TIP31A.3 (E), TIP32A.3 (E)
unnamed: AUDIOOUTLEFT.TP, C5.-
unnamed: 7809CT.IN, C2.+, D3.C
unnamed: AUDIOINLEFT.TP, IC1.3 (+IN)
unnamed: 7809CT.OUT, C1.+, IC1.6 (VS), IC2.6 (VS), R2.1, TIP31A.2 (C), TIP31A1.2 (C)
unnamed: C3.-, C4.-, IC1.5 (OUT)
unnamed: LED1.A, R2.2
unnamed: 12V.TP, D3.A
unnamed: C6.-, IC1.7 (BYPASS)
unnamed: C7.2, IC1.8 (GAIN), R3.2
unnamed: AUDIOINRIGHT.TP, IC2.3 (+IN)
unnamed: C7.1, IC1.1 (GAIN), R3.1
unnamed: C10.+, TIP31A1.3 (E), TIP32A1.3 (E)
unnamed: C8.+, D5.C, R4.1, TIP32A1.1 (B)
unnamed: C9.+, D4.A, TIP31A1.1 (B)
unnamed: D4.C, D5.A
unnamed: AUDIOOUTRIGHT.TP, C10.-
unnamed: C8.-, C9.-, IC2.5 (OUT)
unnamed: 7809CT.GND, C1.-, C2.-, C6.+, C12.+, GND.TP, IC1.2 (-IN), IC1.4 (GND), IC2.2 (-IN), IC2.4 (GND), LED1.K (C), R1.1, R4.2, TIP32A.2 (C), TIP32A1.2 (C)
unnamed: C11.2, IC2.8 (GAIN), R5.1
unnamed: C11.1, IC2.1 (GAIN), R5.2
unnamed: C12.-, IC2.7 (BYPASS)

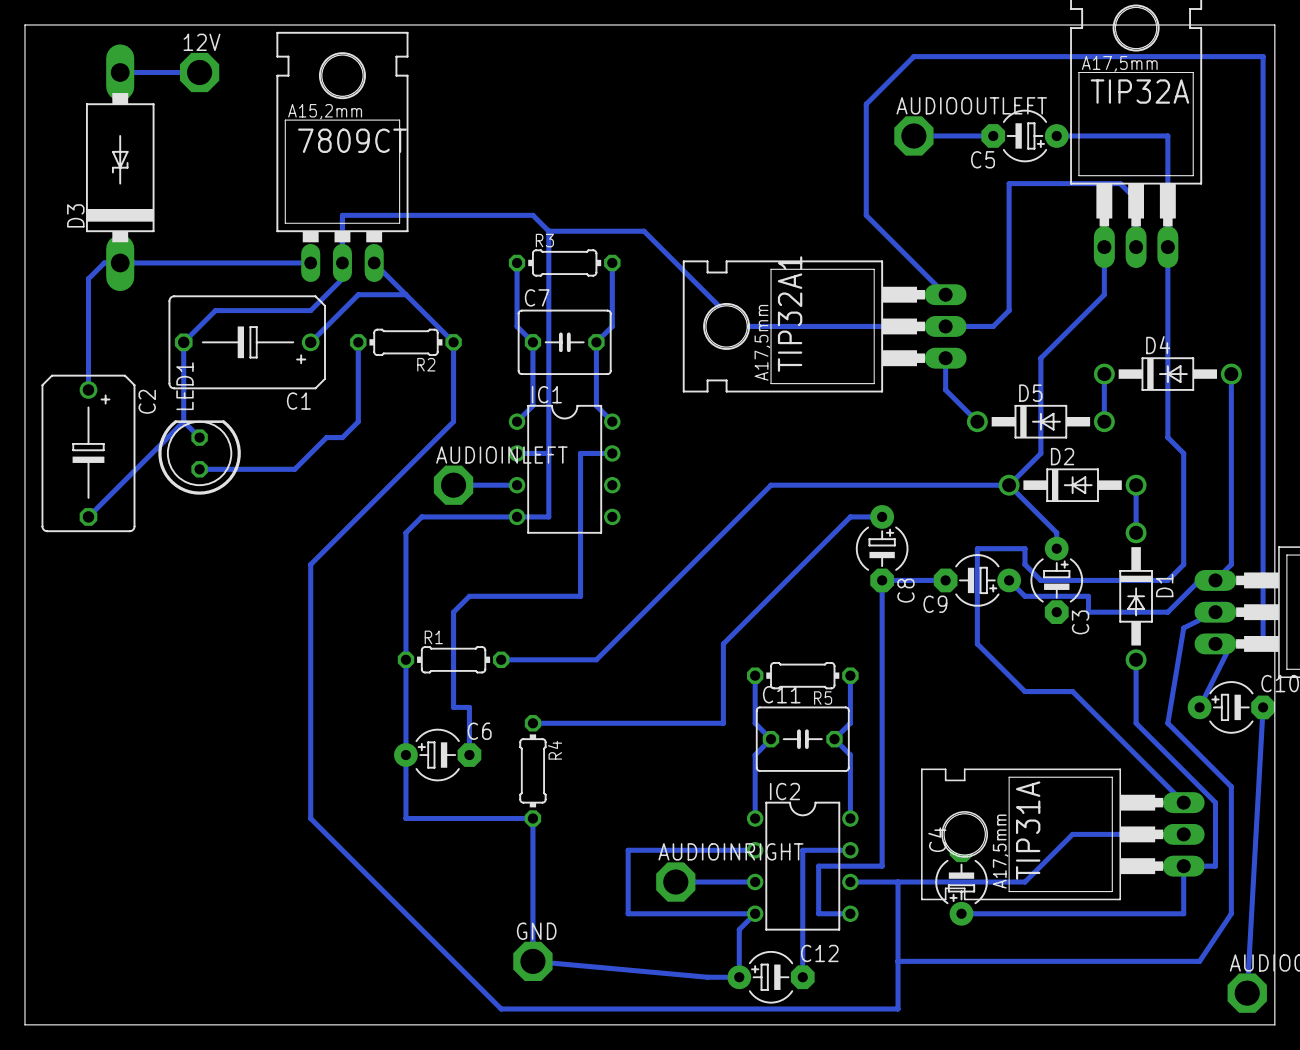
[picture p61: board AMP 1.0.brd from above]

Board: 2 copper layers, 100.0 x 80.0 mm, 36 parts (0 on the bottom side), 25 nets.

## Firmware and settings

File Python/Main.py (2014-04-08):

import pygame, random, sys, math,time,commands,os
from pygame.locals import *
import cProfile
import Reactor as rec
import Brence as br
import Decay
import smbus






def Main():
    ################ Pygame Init
    pygame.init()
    fpsclock = pygame.time.Clock()
    WindowSurface = pygame.display.set_mode((640,480))
    pygame.display.set_caption("Pygame Test ")
    d = Decay.Decay()
    bus = smbus.SMBus(1)
    ADC = os.system("i2cset -y 1 0x48 0x01 0x80E0 w")

    ####################    Pygame Declarations
    testSurface = pygame.image.load("test.png")
    MouseSurface = pygame.Surface((32, 32), 0, 8).convert_alpha()
    MouseSurface.fill((0,100,0,0))
    #MouseSurface.convert_alpha()
    pygame.draw.line(MouseSurface,(0,255,0),(16,0),(16,32),1)
    pygame.draw.line(MouseSurface,(0,255,0),(0,16),(32,16),1)

    ############################# Classes
 
        
    
    #################### Declarations
 
    lines = [0.0]*400
    red = pygame.Color(255,0,0)
    green = pygame.Color(0,255,0)
    blue = pygame.Color(0,0,255)
    white = pygame.Color(255,255,255)
    black = pygame.Color(0,0,0)
    mousex, mousey = 0,0
    font = pygame.font.Font("freesansbold.ttf",12)
    run = 1
    
    ######################## Non-Reactor specific functions
    def keyPressed(inputKey):
        keysPressed = pygame.key.get_pressed()
        if keysPressed[inputKey]:
            return True
        else:
            return False
    
    ######################## Main Loop
    while run:
        ############## Window
        WindowSurface.fill(black) # Screen Redraw
        #pygame.draw.polygon(WindowSurface,red,((100,0),(100,200),(150,175)))
        #PixArr = pygame.PixelArray(WindowSurface)
        #for x in range(100,600,10):
        #    for y in range(100,400,10):
        #        WindowSurface.blit(testSurface,(x,y))
                #PixArr[x][y] = pygame.Color(random.randint(0,255),random.randint(0,255),random.randint(0,255))
        #del PixArr
        
        ###################Reactor update

        ADC = commands.getoutput("i2cget -y 1 0x48 0x00 w")
        #print "ADC: ",ADC
        try:
            ADCNormalized = int(ADC,16)/655.35#327.675
        except:
            print "I2c Error"
            ADCNormalized = 0
        #print ADCNormalized
        lines.insert(0,mousex/48)
        lines = lines[:400]
        tm = time.time()*50
        rec.Draw_Chart(WindowSurface,10,10,400,200,lines,(0,100,0,100),(255,100,0),(255,255,255),3)
  
        ############################# Event dling
        for event in pygame.event.get():
            if event.type == QUIT:
                run = 0
                break
            if event.type == MOUSEMOTION:
                mousex, mousey = event.pos
            if event.type == KEYDOWN:
                if event.key == K_ESCAPE:
                    run = 0
                    break
        ######################### Pygame drawing
        WindowSurface.blit(MouseSurface,(mousex-16,mousey-16))
        WindowSurface.blit(font.render(str((mousex,mousey)),1,(100,100,100)),(mousex+10,mousey))
        WindowSurface.blit(font.render("ADC: "+str(ADC)+" "+str(ADCNormalized),1,(100,255,100)),(10,40))
        pygame.display.update()
        fpsclock.tick(50)
    pygame.quit()
    #raw_input("Pres Enter to exit...")

Main()
#cProfile.run("Main()")

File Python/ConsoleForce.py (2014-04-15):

import  random, sys, math,time,commands,os
import smbus

address = 0x49 # Address of ADC
bus = smbus.SMBus(1) # connect to IIC line # 1
bus.write_word_data(address,0x01,0x80E0) # Default setup
wait = .2
while 1:
	readingraw = bus.read_word_data(address,0x00)
	reading = int(readingraw/256)&0xff        
	reading += (readingraw*256)&0xff00
	#print reading, hex(reading), hex(readingraw)
	print 
	try:
	    ADCNormalized = reading*2/655.35
	except:
	    print "I2c Error"
	    ADCNormalized = 0
	print ADCNormalized,
	if ADCNormalized < 3:
        	for i in range(int(ADCNormalized*10)):
			sys.stdout.write("#")
	time.sleep(wait)

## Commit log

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2013-11-11 Added a Bill Of Materials.
    [BOM.xlsx]
2013-11-12 Updated the BOM to include categories and a pie chart. Waiting on links.
    [BOM.xlsx]
2013-11-13 Added some Solidworks models
    [Deck.SLDPRT, Statics.xlsx, Top Truss.SLDASM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]
2013-11-20 Added a powerpoint for GPIO pins on the RPi
2013-11-20 Not sure what this is
    [BOM.xlsx, Deck.SLDPRT, Statics.xlsx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]
2013-11-20 Added some stuff to the BOM
    [BOM.xlsx]
2013-11-20 Updated BOM
    Added Rasberry Pi, Monitor, and pressure sensor.
    [BOM.xlsx]
2013-12-09 See Extended
    Added to BOM
    Added a bunch of stuff for the presentation
    [BOM.xlsx, gaant.xlsx]
2013-12-11 Small tweaking needed, and Notes
    [gaant.xlsx]
2014-01-13 Made a Solidworks model of the frame. new Folder structure
    [Aluminum crush plate.SLDPRT, BOM.xlsx, Bottom base beam.SLDPRT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]
2014-01-20 Added some stuff
    [2ft foot beam.SLDPRT, BOM.xlsx, Extruded 2x2x.25.SLDPRT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]
2014-01-22 Worked on the frame. Optimized frame. Bom updated
    [2ft foot beam.SLDPRT, Assem1.SLDASM, BOM.xlsx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]
2014-01-22 Moved files around.
    [gaant.xlsx]
2014-01-22 Added a folder for subsystems. Started work on transcribing the hydraulic subsystem diagram from my notebook to Powerpoint.
2014-01-23 Finished Hydraulic Design Updated BOM.xlsx with new parts
    [BOM.xlsx]
2014-01-25 Updated the BOM.xlsx Started on a Force Sensor Diagram
    [BOM.xlsx, Hydraulics.xlsx]
2014-01-28 Added a filter to the Hydraulic.pptx Design added a steel BOM.txt converted the frame reports to PDF. Deleted the extra Solidworks folder. (Some files are still read only and I can't delete them.)
    [Assem1.SLDASM, BOM.xlsx, Copy of BOM.xlsx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]
2014-01-28 Added steel lists to the bom.
    [BOM.xlsx]
2014-01-28 Updated the BOM. Deleted the extra solidworks folder
    [Aluminum crush plate.SLDPRT, BOM.xlsx, Bottom base beam.SLDPRT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]
2014-01-28 Updated BOM to have shipping Updated hydraulics to include filter
    [BOM.xlsx]
2014-02-03 Updated BOM.xlsx
    Did some statics on the Plate to see how strong it is.
    [BOM.xlsx, Statics.xlsx]
2014-02-08 Found couplings for motor and pump. Unsure of pump keyway size, so got the larger option. Added Thumbs.db to the .gitignore file.
    [BOM.xlsx]
2014-02-09 Updated the BOM: Added 7 segments Added a i2d driver for 7 segments Sorted by who should order
    Working on presentation. Needs a lot of work.
    [BOM.xlsx]
2014-02-09 Made a page on the BOM for the presentation. (Removed links and shrunk the page) Presentation is done except for the electrical slide.
    [BOM.xlsx]
2014-02-09 Added an eagle directory. Added a custom eagle library for the 4" 7 segment and the I2C driver Added a project for the Load Display
    [Single Cell.sch]
2014-02-10 Added some eagle files
    [ADC LOG.xlsx, BOM.xlsx, Crunching_FFTs_MAX1420.xls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]
2014-02-10 Added a 5V regulator
    [BOM.xlsx, Single Cell.brd, Single Cell.sch]
2014-02-10 Added a spreadsheet with stuff to order.
    [BOM.xlsx, FEB 10 order.xlsx]
2014-02-13 Broke the BOM into individual files for Bob and Geoff to order stuff
    [2x2 foot gussetts.SLDPRT, BOM.xlsx, FEB 11 Bob.xlsx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]
2014-02-13 Updated Steel list
    [BOM.xlsx]
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2014-02-25 Added a lot of eagle stuff
    [BOM.xlsx, Pump motor mount standoff.SLDPRT, Single Cell.sch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]
2014-02-25 IIC drivers do not work the way i want the too.
    [IIC_Test.ino]
2014-03-11 Did a lot of work
    [2ft foot beam.SLDDRW, Crossbeam 2.0.SLDDRW, Crossbeam 2.0.SLDPRT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]
2014-03-20 Added a bunch of eagle files. Working on PowerPoint
    [Part1.SLDPRT, bracket assembly.SLDASM, motor face analog.SLDDRW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]
2014-03-24 Modified the bracket file. Added the presentation.
    [bracket assembly.SLDASM, bracket assembly.SLDDRW, motor face analog.SLDDRW]
2014-03-24 Added the 7 segment boards
    [7-SEG schematic.sch]
2014-03-28 Added all the python scripts for the GUI
    [Decay.csv, Decay.ods, Nuclear Isotopes.ods]
2014-04-03 Added a bunch of local files
    [7-SEG schematic.brd, 7-Seg jumper.brd, 7-Seg jumper.sch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]
2014-04-04 Added a bunch of stuff to make the new 7 segment boards.
    [Single Cell.brd, Single Cell.sch]
2014-04-08 Fixed some errors on the IIC section of the master file.
    [Master.py]
2014-04-08 Finished the board for the 7 segments.
    [Single Cell.brd, Single Cell.sch]
2014-04-08 Merge remote-tracking branch 'remotes/origin/Panic_Mode_Ben' into HEAD
    Conflicts:
    Python/Master.py
    [Single Cell.brd, Single Cell.sch]
2014-04-14 Changed the distance address to the pressure address for testing and fixed bugs.
    [Master.py]
2014-04-14 Working on making the sortware work. Have decided to ignore the 7 segments for now.
    [Decay.csv, Decay.ods, Nuclear Isotopes.ods]
2014-04-14 Attempting to save github password
    [Decay.csv, Decay.ods, Nuclear Isotopes.ods]
2014-04-15 Scalling is off, but the graph works really well. also, noise is minimal.
    [Master.py]
2014-04-15 Found the bug. Was adding 1 to the max data, but often the data was really small. Fixed
    [Master.py]
2014-04-15 Having the program display raw ADC values, so I can calibrate
2014-04-15 Graph is working. having troulbe with calibrating the force
2014-04-16 Tag text is working. Do want to make the tag switch sides
2014-04-16 Draw Graph functuion is just about finshed. Do want to impliment not drawing every frame.
2014-04-16 Trying with fullscreen 1024x768. About the smallest size I think is reasonable. (Wrong aspect ratio)
    [Master.py]
2014-04-16 poling thread had no limit. Fixed
    [Master.py]
2014-04-17 Found out that it was adding every sample, now using 10x averaging. Also, 500 lines = ~.065 seconds to draw, so is about max
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2014-04-17 Calibration ready, but there is a lot of noise.
    [Master.py]
2014-04-17 87 lb of noise. thats bad.
    [Master.py]
2014-04-17 ready for calibration. Unfortunatly, there is a lot of load noise. about 30lb's worth.
    [Master.py]
2014-04-17 Pi crashed due to vibrations on HDD. I/O error
    [Master.py]
2014-04-18 Calibration data added
    [Calibrating the Strig pot.xlsx, Calibration.xlsx]
2014-04-18 New calibration numbers
    [Calibration.xlsx]
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

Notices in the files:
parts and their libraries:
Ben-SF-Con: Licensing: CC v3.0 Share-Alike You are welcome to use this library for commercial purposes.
